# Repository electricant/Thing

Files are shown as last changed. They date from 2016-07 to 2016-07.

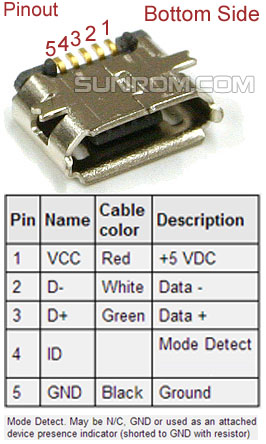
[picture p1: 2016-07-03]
board/datasheet/micro-usb-pinout.jpg

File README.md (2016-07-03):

# Thing

Final projects for Robotics exam.

# Objectives

The goal of this project is designing a board to control 5 servomotors,
one for each finger of a [robotic hand](http://inmoov.fr/hand-and-forarm/).
The heart of the project is an atXmega microcontoller which should be able
to set both the current, the angle and the speed of each servo individually.
The hand is also capable of holding things with a user-specified force.

Everything is battery powered and commands can be sent via a WiFi link or
through an USB port. A [ROS](http://www.ros.org/) module will be provided for 
integration with existing or new robotics projects.

A programmer is included within the board for easy firmware upgrade.

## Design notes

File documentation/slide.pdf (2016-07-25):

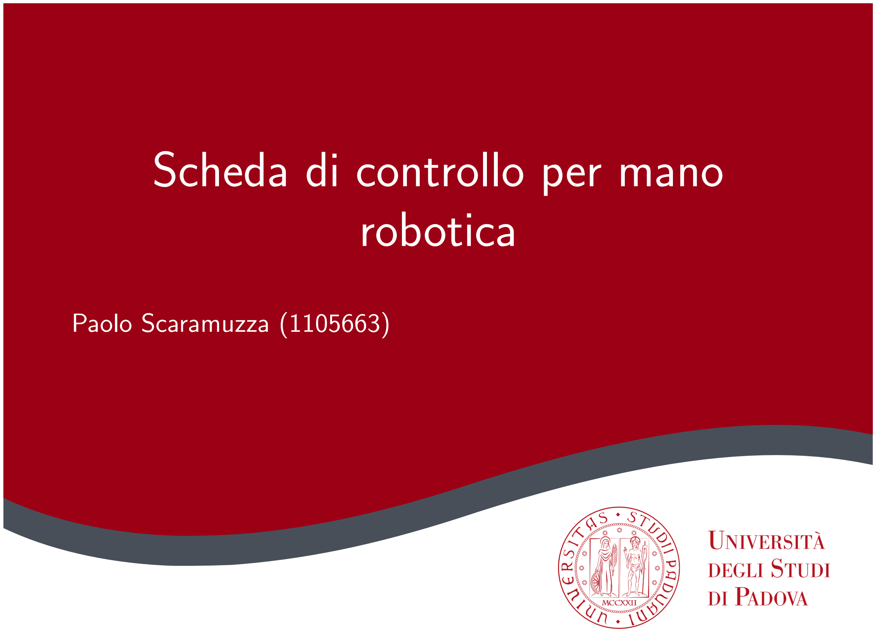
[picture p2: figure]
Scheda di controllo per mano robotica; Paolo Scaramuzza (1105663)

## Contenuti

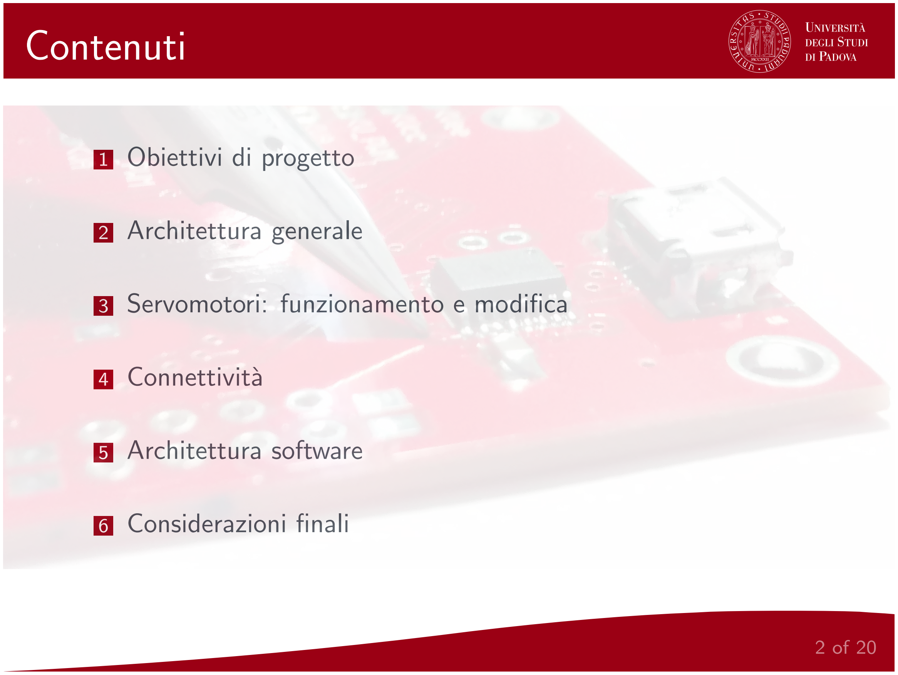
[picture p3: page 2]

1 | Obiettivi di progetto
2 | Architettura generale
3 | Servomotori: funzionamento e modifica
4 | Connettivit`a
5 | Architettura software
6 | Considerazioni finali

## Obiettivi di progetto

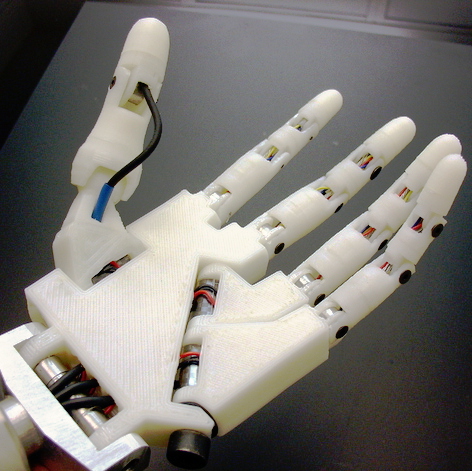
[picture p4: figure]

Controllo di angolo, velocit`a e forza di 5 servomotori
Rate di aggiornamento
≥ 100Hz

Alimentazione a batteria
Controllo WiFi e USB
Facilit`a d’uso e
programmazione

## Architettura generale

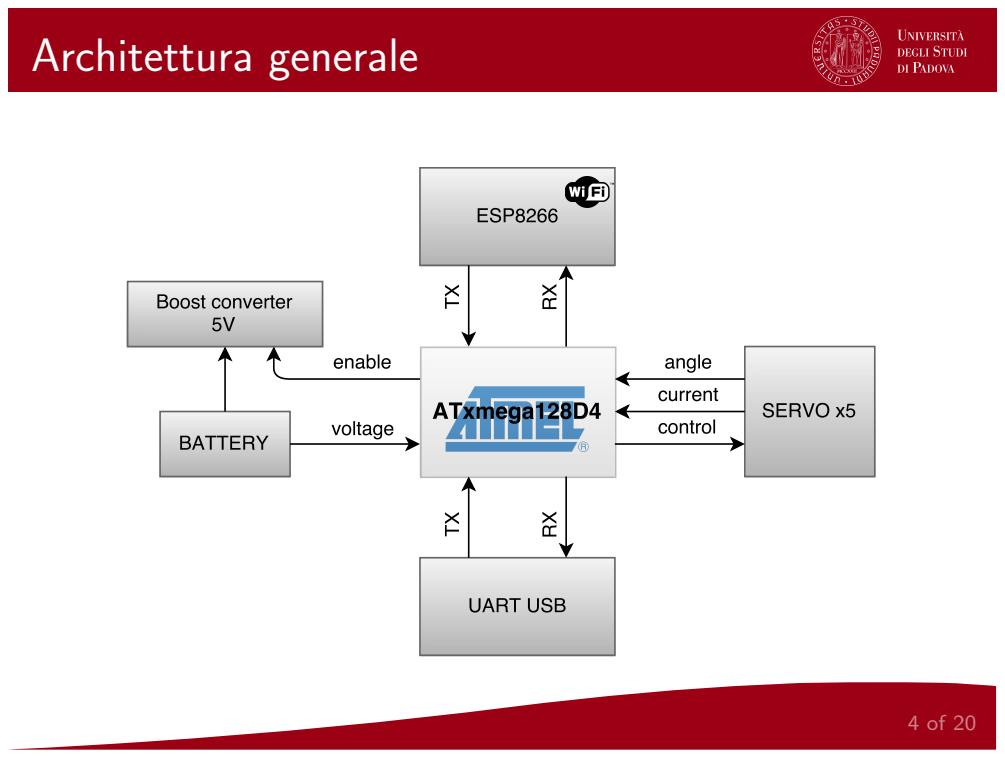
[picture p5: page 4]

## Servomotori - Funzionamento

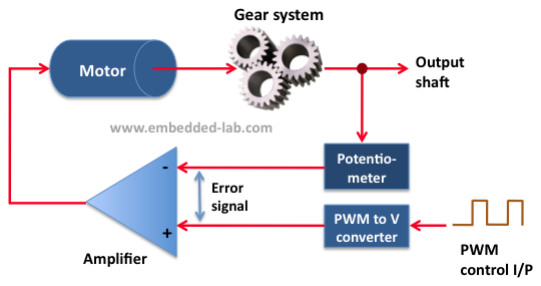
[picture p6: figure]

Sistema in feedback
Facile controllo
Non conosco l’angolo effettivo

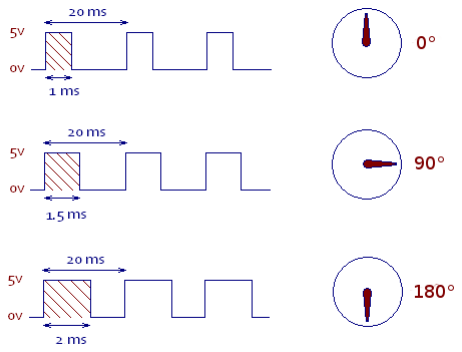
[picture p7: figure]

Non conosco la corrente assorbita (sforzo)

## Servomotori - Lettura dell’angolo

IDEA: loop di controllo esterno (microcontrollore)

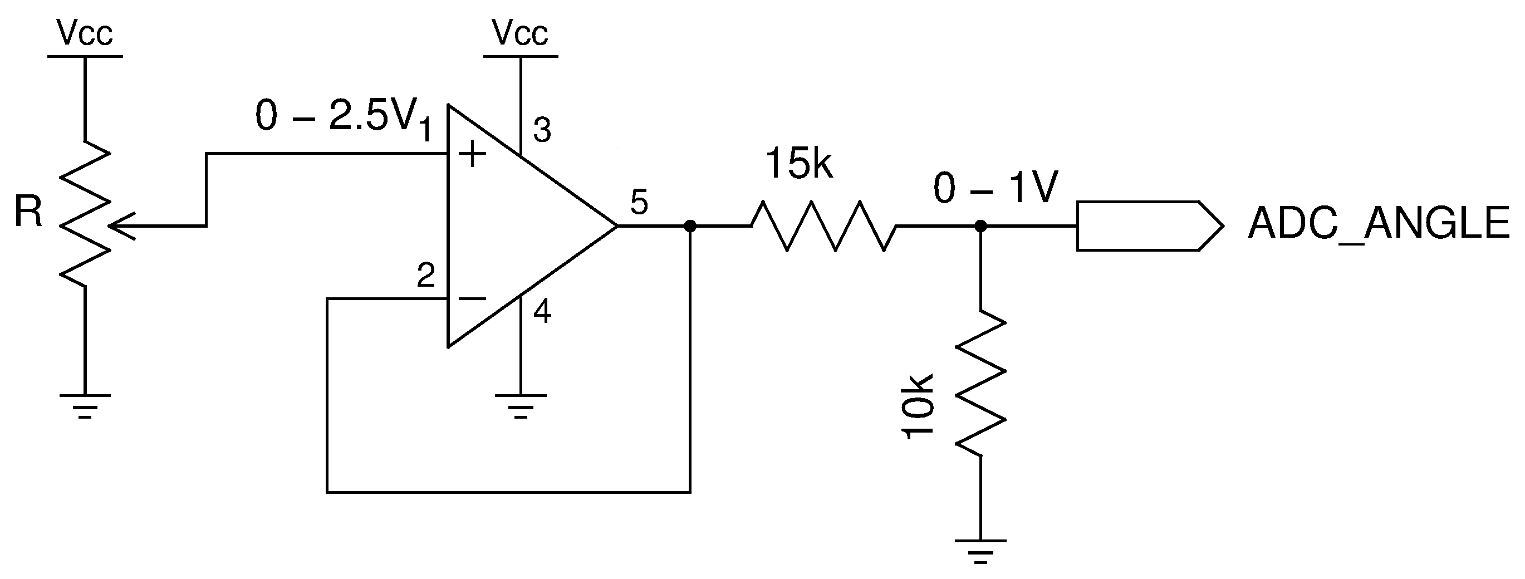
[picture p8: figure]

VADC = VA ·

10k
10k + 15k

=

α
180◦

Non assorbire corrente dal potenziometro!

## Servomotori - Lettura della corrente

IDEA: loop di controllo esterno (microcontrollore)

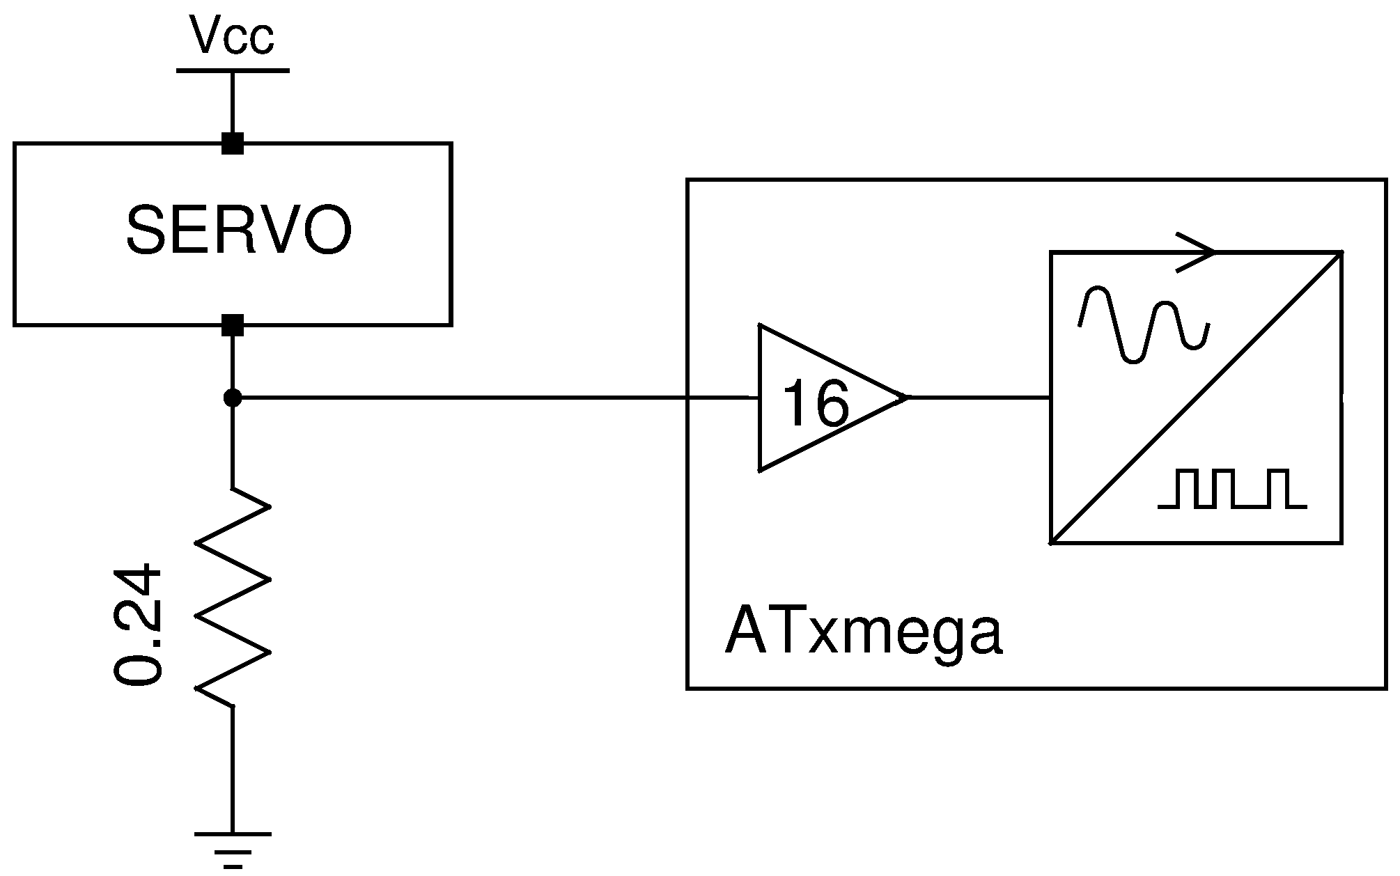
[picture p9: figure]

VADC = 16 · 0.24 · I

s ≈

1V
256
- I

(mA)
s

Errore sistematico (correggibile) pari all’1, 54%

## ESP8266

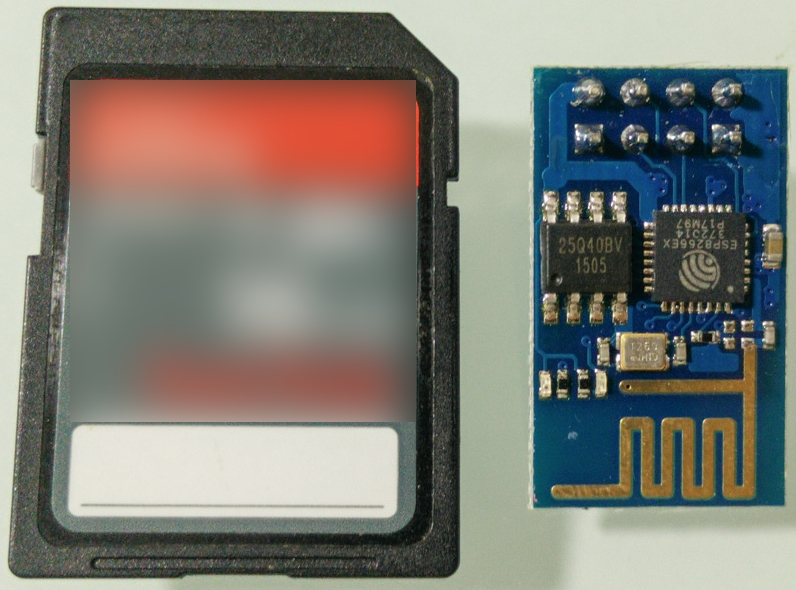
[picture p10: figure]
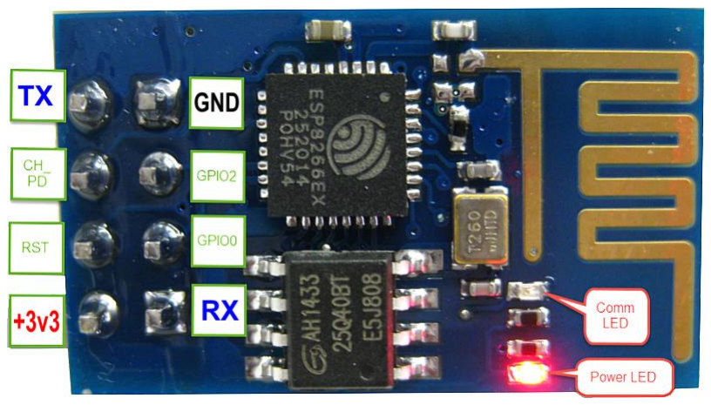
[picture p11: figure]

Prodotta da Espressif (Shanghai)

Molto diffusa tra i makers
IEEE 802.11 b/g/n Wi-Fi con stack TCP/IP completo 80 MHz 32bit RISC CPU (Tensilica Xtensa LX106)

## ESP8266 - Funzionamento e comandi

Alimentazione: 2,5 - 3,3V 150mA (≈ 0, 5W )

Interfaccia seriale 115200baud (modificabile)

Set di comandi Hayes (AT - attention)

AT+<comando><CR><LF>

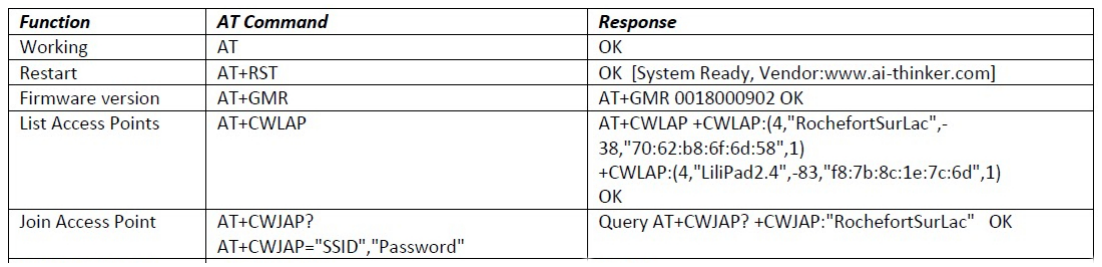
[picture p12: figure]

## Adattatore seriale USB

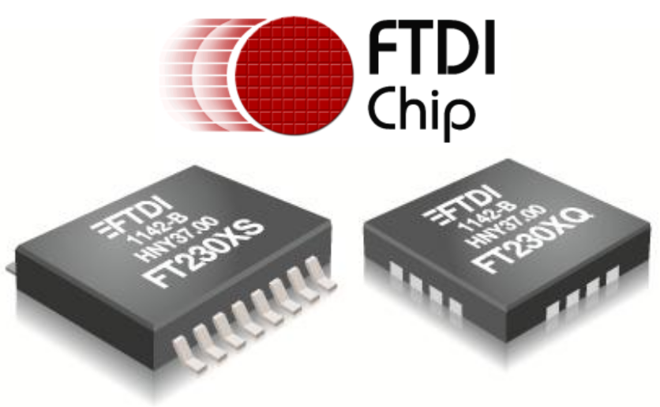
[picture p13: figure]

Pochi componenti esterni (capacit`a di bypass)

Alimentazione: 1,8 - 5V 8mA (≈ 40mW )

Da 300 a 3M baud con o senza parit`a

USB product name e manufacturer configurabili

## Scheda elettrica

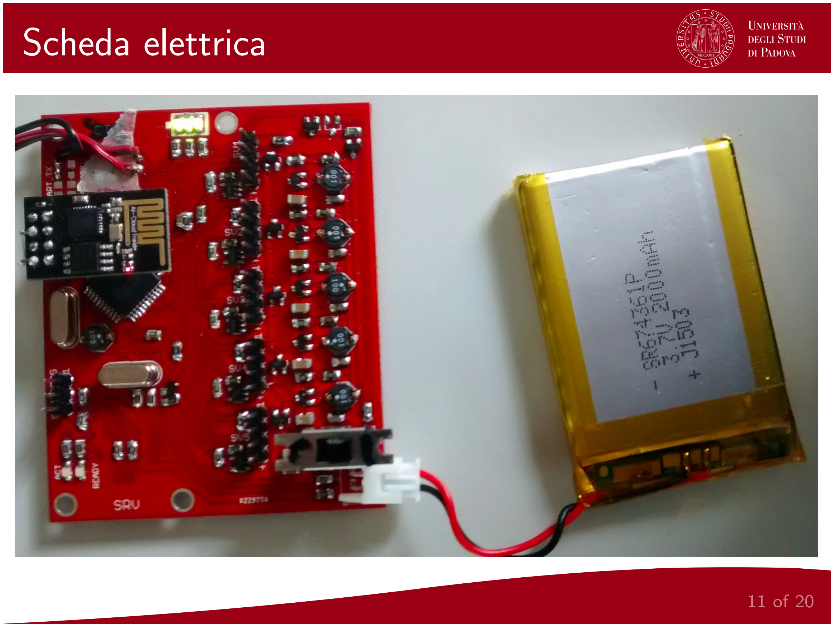
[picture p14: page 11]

## Architettura software

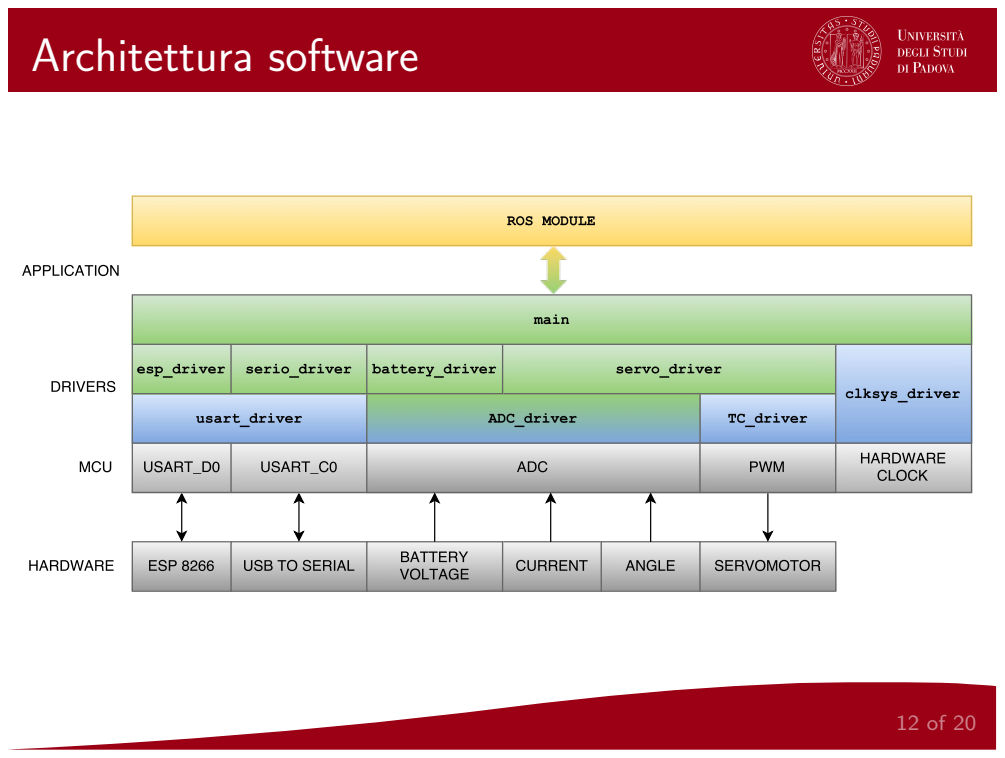
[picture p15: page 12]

## esp driver

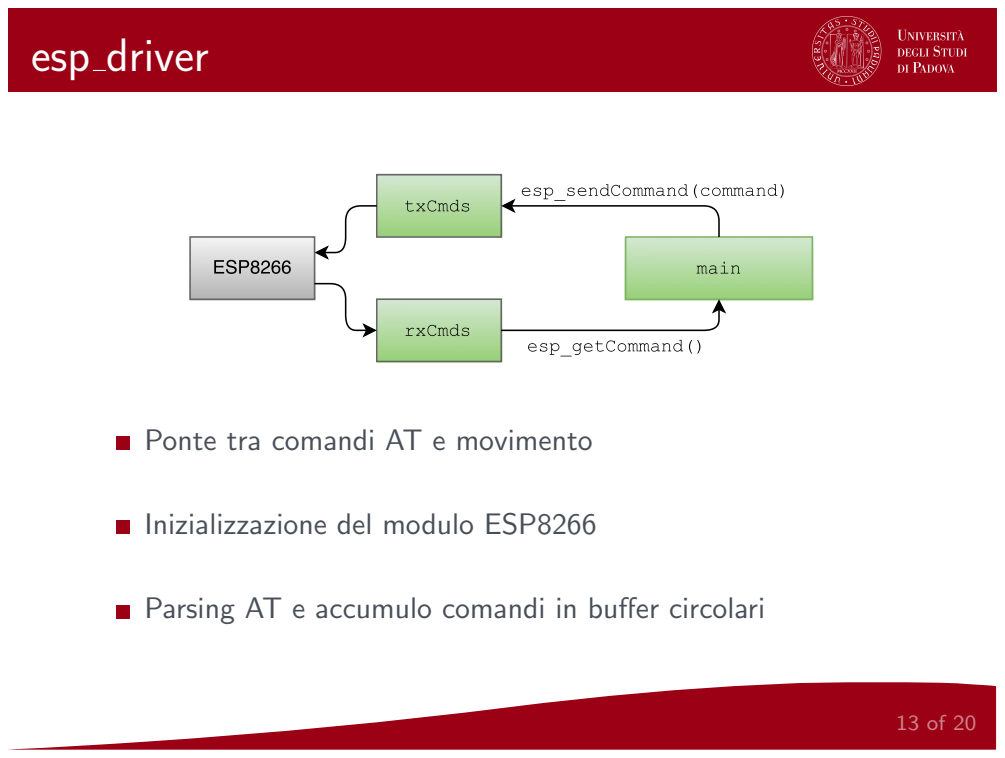
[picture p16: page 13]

Ponte tra comandi AT e movimento

Inizializzazione del modulo ESP8266

Parsing AT e accumulo comandi in buffer circolari

## esp driver - Comandi

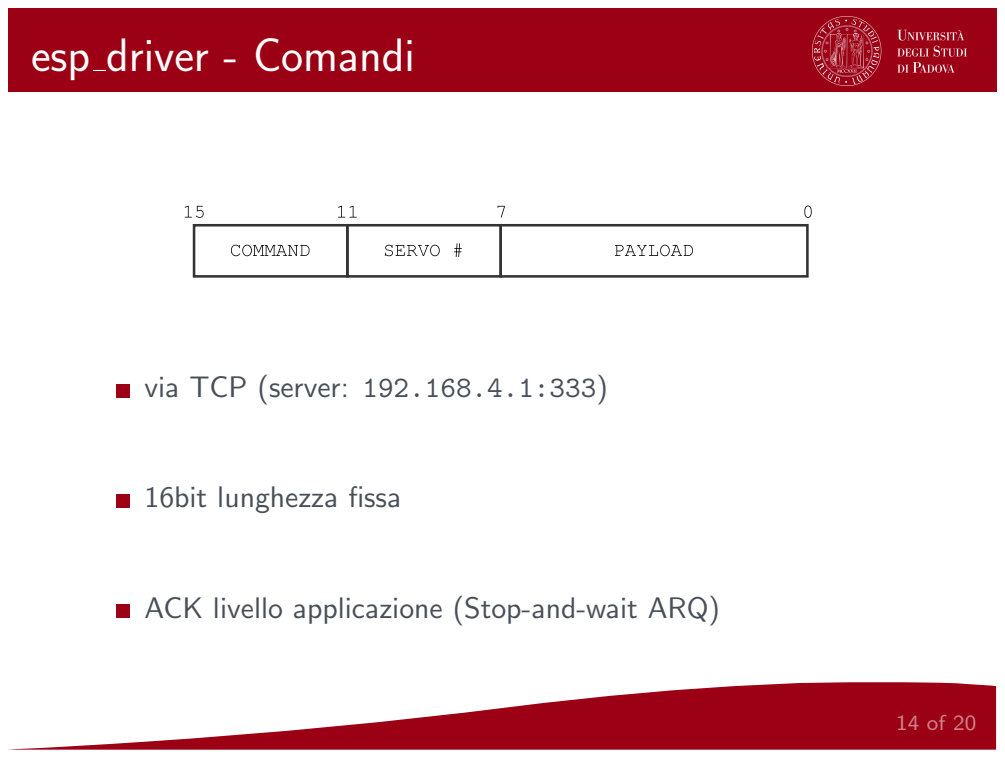
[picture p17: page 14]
16bit lunghezza fissa

via TCP (server: 192.168.4.1:333)

ACK livello applicazione (Stop-and-wait ARQ)

## serio driver

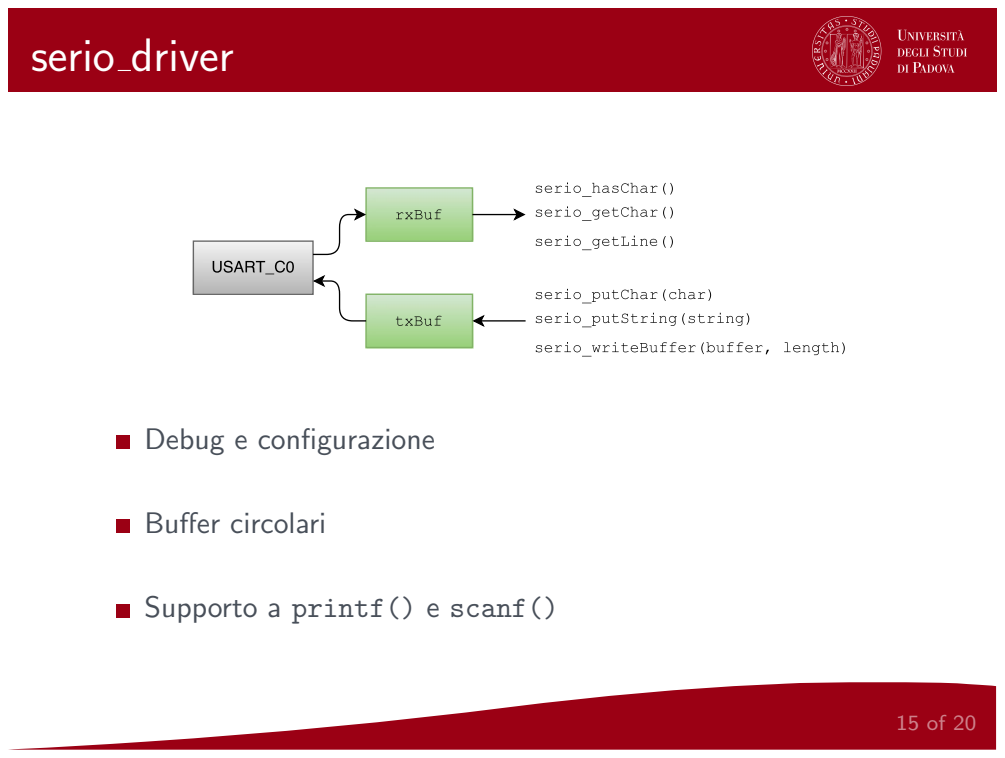
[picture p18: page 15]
Debug e configurazione; Buffer circolari

Supporto a printf() e scanf()

## battery driver

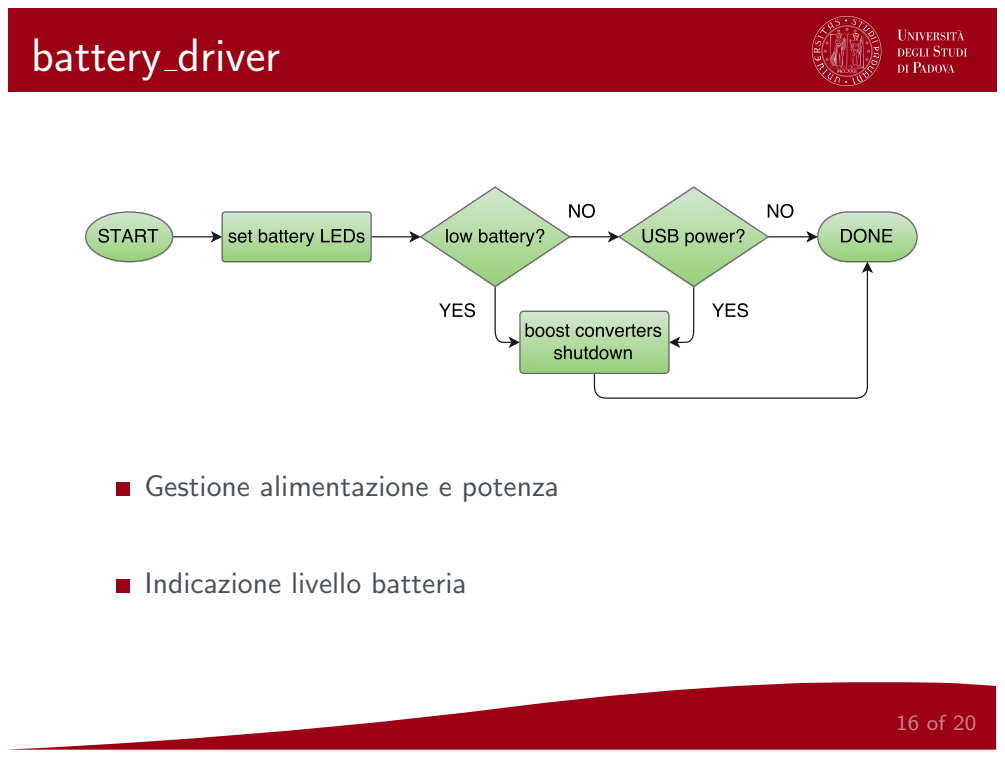
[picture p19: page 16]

Gestione alimentazione e potenza

Indicazione livello batteria

## adc driver

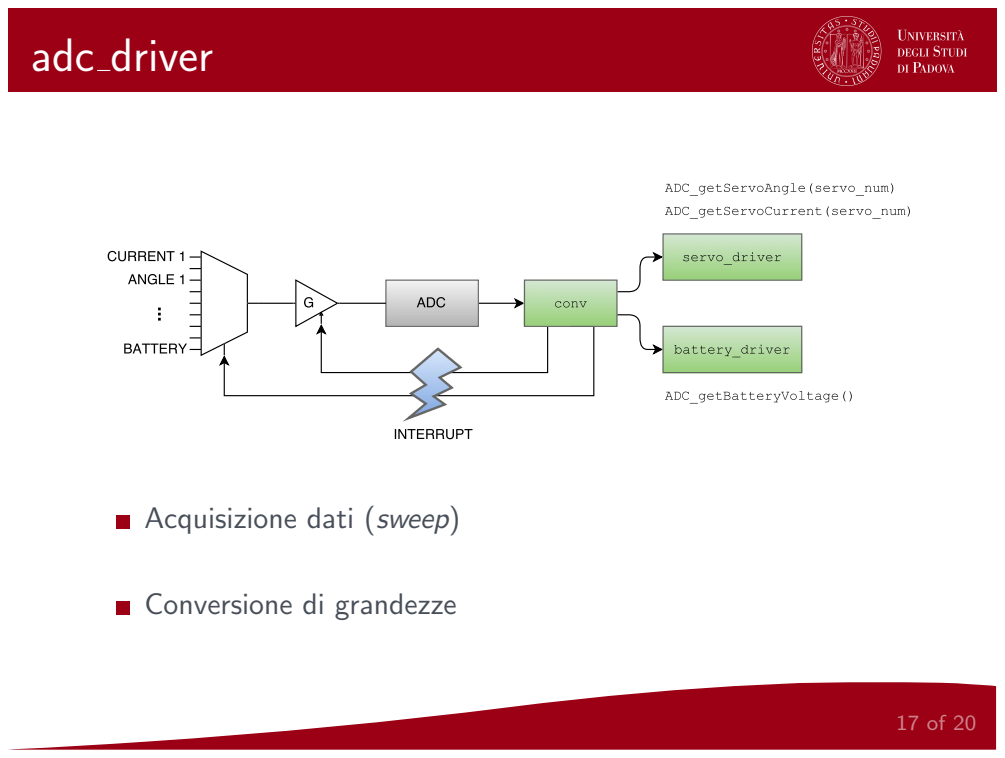
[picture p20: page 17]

Acquisizione dati (sweep)

Conversione di grandezze

## servo driver

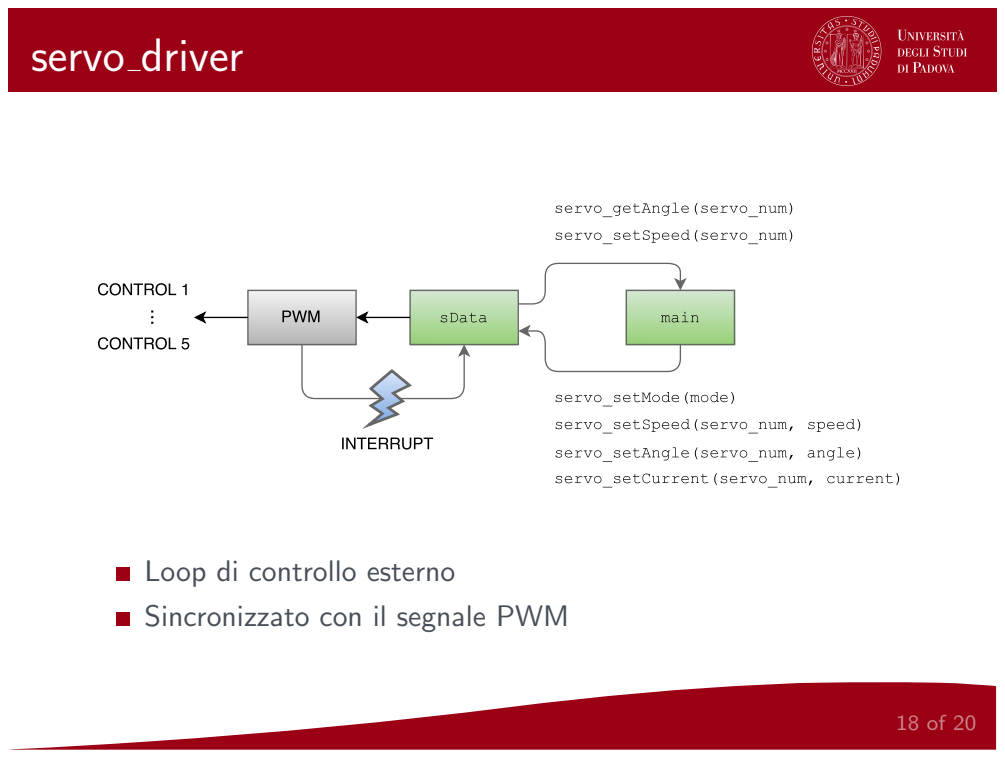
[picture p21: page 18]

Loop di controllo esterno
Sincronizzato con il segnale PWM

## servo driver - Modalit`a operative

Singolo motore: Forza (corrente), velocit`a e angolo

Globalmente:

FOLLOW −→ ”mano morta”

ANGLE −→ raggiunge una posizione con velocit`a imposta

HOLD −→ stringe oggetti con forza nota

## Conclusioni

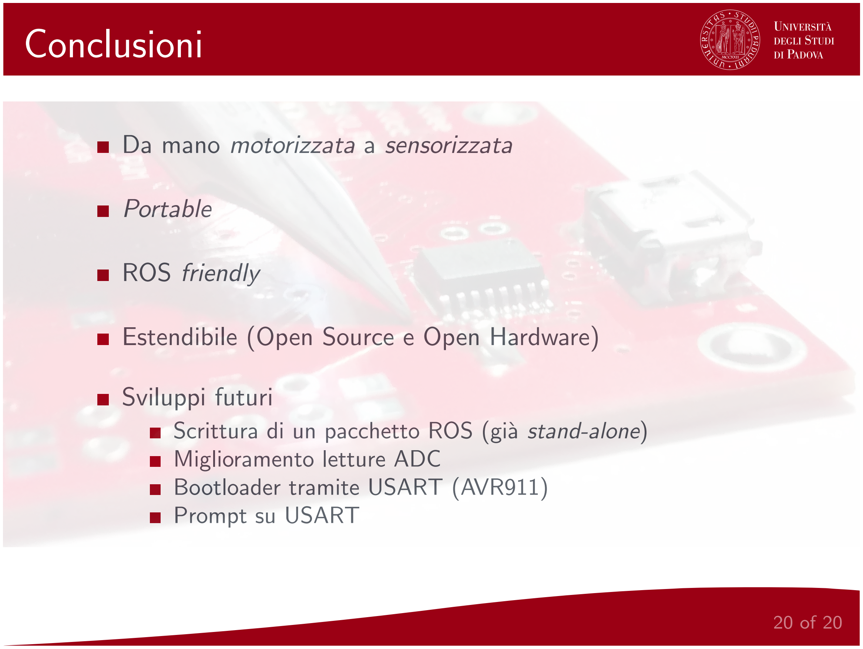
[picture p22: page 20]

Da mano motorizzata a sensorizzata

Portable

ROS friendly

Estendibile (Open Source e Open Hardware)

Sviluppi futuri
Scrittura di un pacchetto ROS (gi`a stand-alone) Miglioramento letture ADC
Bootloader tramite USART (AVR911)
Prompt su USART

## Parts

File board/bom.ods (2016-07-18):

Oggetto | Descrizione | Quantità richiesta | Acquistati | Costo unitario | Link | Note | Costo totale | Presente in laboratorio
 | batteria 3,7V | 1 | 1 | 14,29 | link (http://it.rs-online.com/web/p/pacchi-batteria-al-litio-ricaricabili/7916460/) | batteria al litio rettangolare 3,7V 2000mAh | 14,29
 | Boost converter 1A | 5 | 6 | 1,02 | link (http://it.rs-online.com/web/p/convertitori-boost/7546402/) | MIC2250 | 6,12
 | condensatore 100nF | 11 | 50 | 0,004 | link (http://it.rs-online.com/web/p/condensatori-ceramici-multistrato/0390990/) | Ne avanzeranno un pochi. | 0,2
 | condensatore 10uF SMD | 8 | 10 | 0,069 | link (http://it.rs-online.com/web/p/condensatori-ceramici-multistrato/6983734/) |  | 0,69 | un sacco da 4,7u
 | condensatori 47pF | 2 | 25 | 0,023 | link (http://it.rs-online.com/web/p/condensatori-ceramici-multistrato/2644270/) | Qui ne avanzeranno di più | 0,575
 | condensatori quarzo 27pF | 4 | 5 | 0,27 | link (http://it.rs-online.com/web/p/condensatori-ceramici-multistrato/6984064/) | Suppongo 5pF di capacità sui piedini. CL= 18pF | 1,35 | si 4
 | connettore batteria maschio | 1 | 5 | 0,114 | link (http://it.rs-online.com/web/p/file-di-contatti-da-pcb/8201582/) | JST-XHP-2 per PCB ad angolo retto (più carino) | 0,57
 | connettore batteria femmina | 1 | 0 | 0 |  | 2 pin, difficile da invertire, già sulla batteria | 0
 | connettore servo femmina filo | tanti | 0 | 0 |  | pin singolo per filo di sensing, usare cavi arduino con presa femmina |  | si tanti
 | connettore servo maschio | 5 | 10 | 0,116 | LINK (http://it.rs-online.com/web/p/file-di-contatti-da-pcb/6812988/) | 4 pin. Scrivere sul PCB la funzione di ciascun PIN | 1,16 | si in abbondanza
 | controller carica batteria | 1 | 5 | 0,51 | link (http://it.rs-online.com/web/p/controller-carica-di-batterie/7386617/) | MCP73831-2 | 2,55
 | convertitore LDO 3,3V | 1 | 25 | 0,122 | link (http://it.rs-online.com/web/p/regolatori-di-tensione-low-dropout/8855980/) | MIC5504-3.3 oppure SP6201EM5-3.3 | 3,05
 | convertitore seriale-usb | 1 | 2 | 1,86 | link (http://it.rs-online.com/web/p/trasmettitori-e-ricevitori-universali-asincroni/7570010/) | FT230XS-R | 3,72
 | diodo shottky 1A | 12 | 20 | 0,039 | link (http://it.rs-online.com/web/p/diodi-rettificatori-e-schottky/0508977/) | package SOT-23 | 0,78
 | ESP8266 | 1 | 0 | 0 |  | Ce lo metto di mio che si fa prima | 0
 | header ICSP | 1 | 5 | 0,304 | link (http://it.rs-online.com/web/p/file-di-contatti-da-pcb/6737503/) | 6pin Header Connector with 2.54mm (100 MIL) spacing (con quelli che avanzano TP UART) | 1,52 | si in abbondanza
 | Induttori boost 10uH | 6 | 10 | 0,288 | link (http://it.rs-online.com/web/p/induttori-avvolti-smd/7381211/) |  | 2,88
 | LED verde | 7 | 50 | 0,05 | linik (http://it.rs-online.com/web/p/led-visibili/6545773/) | TX + RX seriale, programmatore e livello batteria | 2,5 | si 5 color rosso
 | microcontrollore AT90USB162 | 1 | 1 | 3,82 | link (http://it.rs-online.com/web/p/microcontroller/7153750/) | per programmare la board via usb. Vedi AVR-ISP-MK2 (https://www.olimex.com/Products/AVR/Programmers/AVR-ISP-MK2/open-source-hardware) | 3,82
 | microcontrollore ATxmega128D4 | 1 | 1 | 4,02 | link (http://it.rs-online.com/web/p/microcontroller/7153873/) |  | 4,02
 | opamp MCP6L01T-E/OT | 5 | 10 | 0,221 | link (http://it.rs-online.com/web/p/amplificatori-operazionali/7386196/) |  | 2,21
 | PCB | 1 | 0 | 0 |  | Ce lo metto di mio che si fa prima | 0
 | porte micro usb | 2 | 5 | 0,426 | link (http://it.rs-online.com/web/p/connettori-micro-usb/7142344/) |  | 2,13
 | quarzo 16MHz | 2 | 10 | 0,167 | link (http://it.rs-online.com/web/p/cristalli/8149440/) | Tutti e due i micro usano un quarzo. Per il principale vedi come si configura e usa | 1,67
 | resistenza 0,24 Ohm 1% | 5 | 5 | 0,182 | link (http://it.rs-online.com/web/p/resistori-smd/7215423/) | sensing di corrente | 0,91 | 8 da 0,1Ohm
 | resistenza 100 Ohm | 9 | 50 | 0,01 | link (http://it.rs-online.com/web/p/resistori-smd/7408978/) | PDI + LED batteria (due in parallelo) | 0,5
 | resistenza 100kOhm | 6 | 50 | 0,01 | link (http://it.rs-online.com/web/p/resistori-smd/2230691/) |  | 0,5
 | resistenza 10kOhm 1% | 12 | 50 | 0,006 | link (http://it.rs-online.com/web/p/resistori-smd/2230584/) |  | 0,3 | si un sacco
 | resistenza 15kOhm 1% | 5 | 50 | 0,016 | link (http://it.rs-online.com/web/p/resistori-smd/7408975/) |  | 0,8 | si un sacco
 | resistenza 18kOhm | 2 | 50 | 0,023 | link (http://it.rs-online.com/web/p/resistori-smd/2230590/) |  | 1,15
 | resistenza 2,2kOhm | 1 | 50 | 0,034 | link+ (http://it.rs-online.com/web/p/resistori-smd/6791207/) |  | 1,7 | si un sacco
 | resistenza 22 Ohm | 2 | 50 | 0,006 | link (http://it.rs-online.com/web/p/resistori-smd/2230203/) |  | 0,3 | si un sacco
 | resistenza 27 Ohm | 2 | 50 | 0,016 | link (http://it.rs-online.com/web/p/resistori-smd/6791187/) |  | 0,8
 | resistenza 330 Ohm | 9 | 50 | 0,017 | link (http://it.rs-online.com/web/p/resistori-smd/7409022/) |  | 0,85
 | resistenza 330kOhm | 1 | 50 | 0,01 | link (http://it.rs-online.com/web/p/resistori-smd/6791272/) |  | 0,5
 | resistenza 33kOhm | 5 | 50 | 0,021 | link (http://it.rs-online.com/web/p/resistori-smd/2230629/) |  | 1,05 | si 3
 | switch batteria | 1 | 1 | 2,49 | link (http://it.rs-online.com/web/p/interruttori-a-slitta/7118385/) | 4 A 20mOhm | 2,49
 | switch programmazione NA | 2 | 0 | 0 |  | RESET + HWB (vedi qui) - Ne porto da casa (http://www.atmel.com/Images/doc7627.pdf) | 0
 | transistor NPN SMD | 1 | 0 | 0 |  | Me lo porto da casa | 0
 |  |  |  |  |  |  | TOTALE:
 |  |  |  |  |  |  | 67,655
 |  |  |  |  |  |  | TOTALE + IVA
 |  |  |  |  |  |  | 82,5391

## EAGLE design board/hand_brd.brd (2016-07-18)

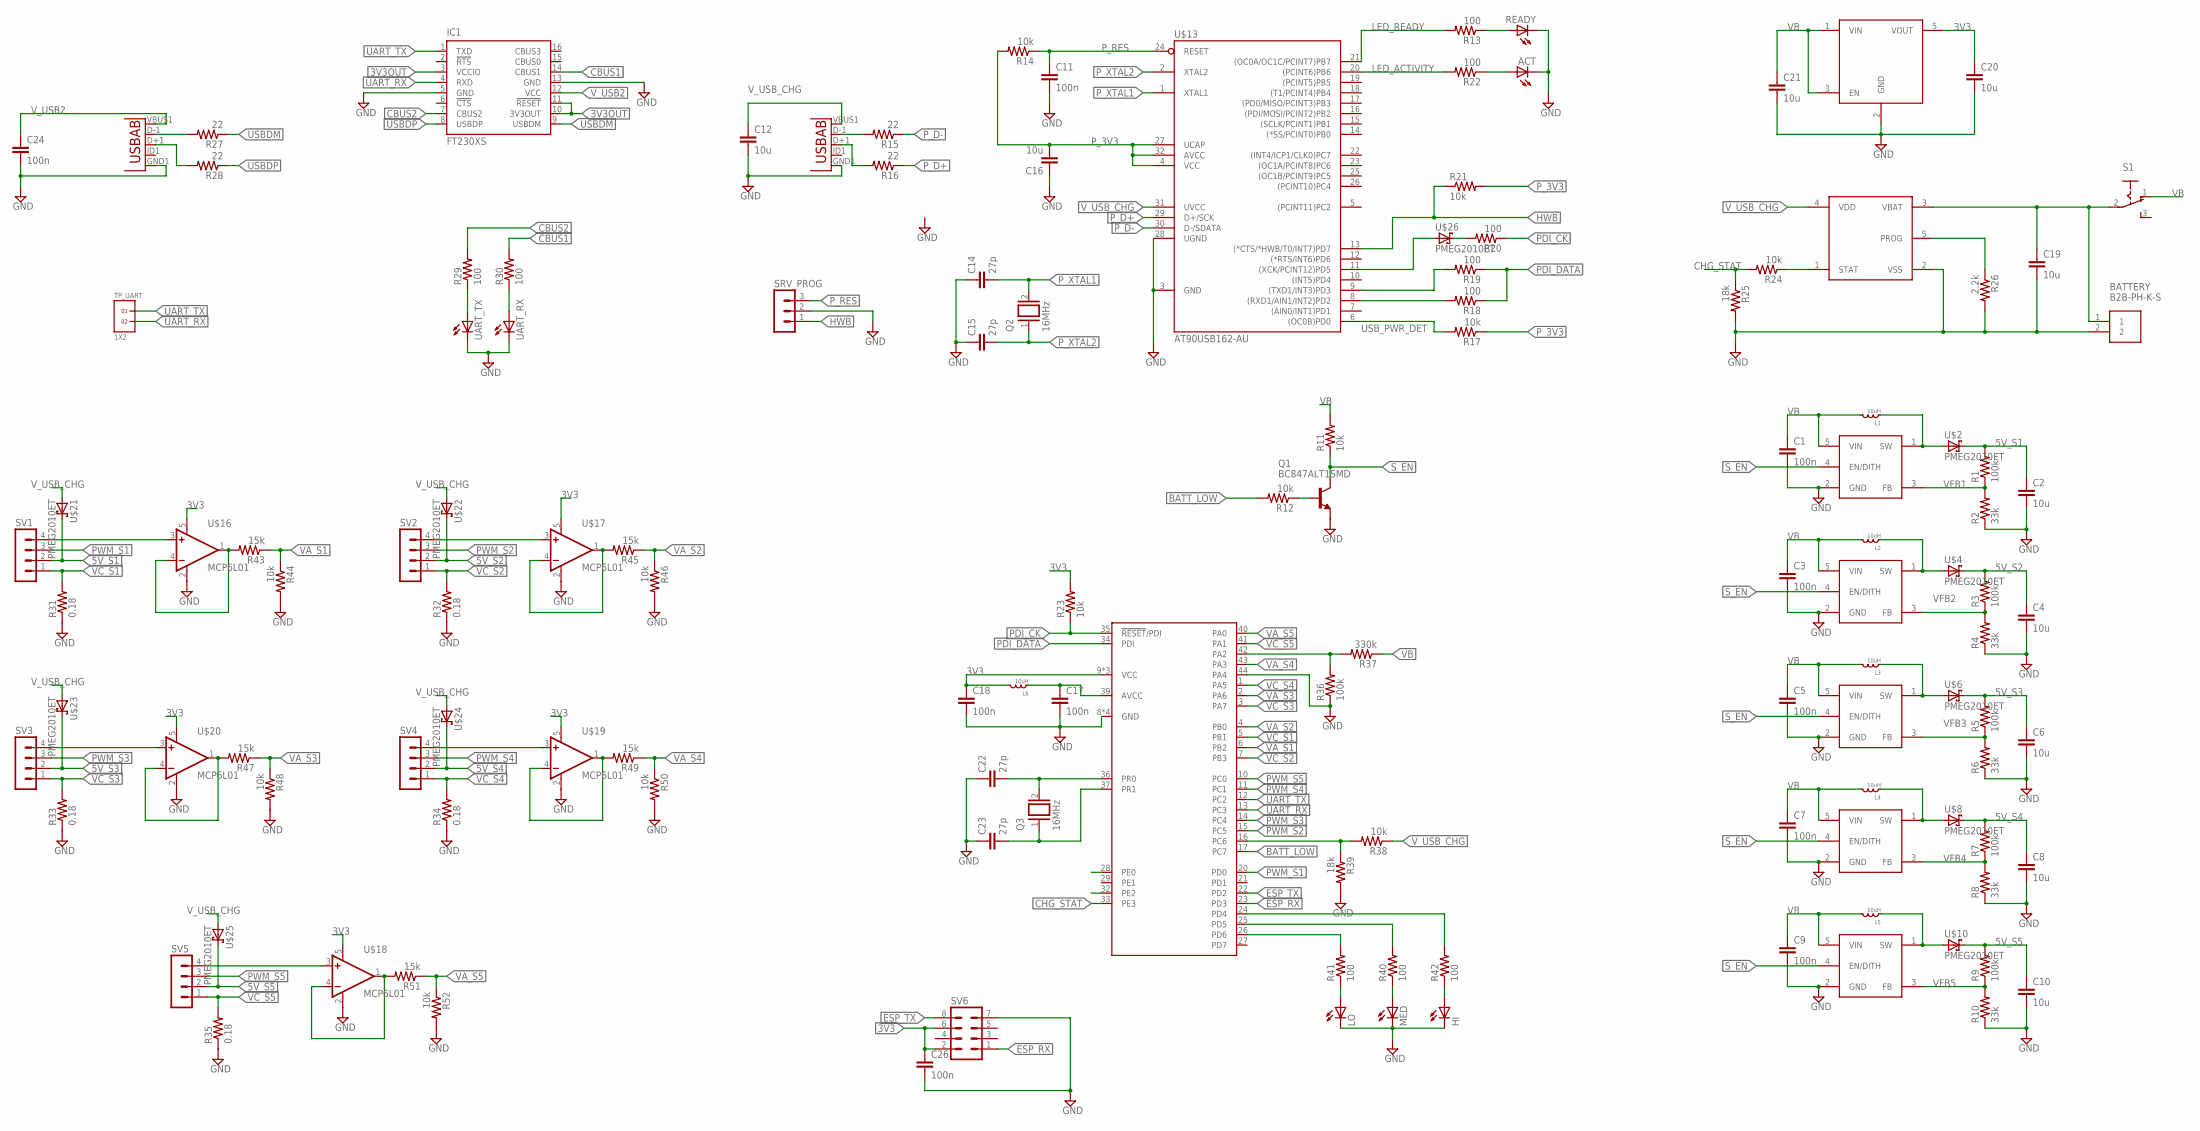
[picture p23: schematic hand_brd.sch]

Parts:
ACT: LEDCHIPLED_0805; CHIPLED_0805
BATTERY: B2B-PH-K-S
C1, C3, C5, C7, C9, C11, C17, C18, C24, C26: 100n; C0805K
C2, C4, C6, C8, C10, C12, C16, C19, C20, C21: 10u; C0805K
C14, C15, C22, C23: 27p; C0805K
HI: LEDCHIPLED_0805; CHIPLED_0805
IC1: FT230XS; SSOP16
L1, L2, L3, L4, L5, L6: 10uH; LTF5022
LO: LEDCHIPLED_0805; CHIPLED_0805
MED: LEDCHIPLED_0805; CHIPLED_0805
Q1: BC847ALT1SMD; SOT23
Q2, Q3: 16MHz; QS
R1, R3, R5, R7, R9, R36: 100k; M0805
R2, R4, R6, R8, R10: 33k; M0805
R11, R12, R14, R17, R21, R23, R24, R38, R44, R46, R48, R50, R52: 10k; M0805
R13, R18, R19, R20, R22, R29, R30, R40, R41, R42: 100; M0805
R15, R16, R27, R28: 22; M0805
R25, R39: 18k; M0805
R26: 2.2k; M0805
R31, R32, R33, R34, R35: 0.18; M0805
R37: 330k; M0805
R43, R45, R47, R49, R51: 15k; M0805
READY: LEDCHIPLED_0805; CHIPLED_0805
S1: 255SB
SRV_PROG: MA03-1
SV1, SV2, SV3, SV4, SV5: MA04-1
SV6: MA04-2
TP_UART: 1X2
U1, U3: USB""; USB-MICRO-SMD
U2: ATXMEGA128D4-AU; TQFP-44A-44
U$1, U$3, U$5, U$7, U$9: MIC2250-2YD5; SOT23-5
U$2, U$4, U$6, U$8, U$10, U$21, U$22, U$23, U$24, U$25, U$26: PMEG2010ET; SOT23
U$13: AT90USB162-AU; TQFP32-08
U$14: MCP73831; SOT23-5
U$15: MIC5504; SOT23-5
U$16, U$17, U$18, U$19, U$20: MCP6L01; SOT23-5
UART_RX: LEDCHIPLED_0805; CHIPLED_0805
UART_TX: LEDCHIPLED_0805; CHIPLED_0805

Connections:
3V3: C18.1, C20.1, C26.1, L6.P$2 (2), R23.2, SV6.2, SV6.6, U2.9 (VCC), U2.19 (VCC), U2.31 (VCC), U$15.5 (VOUT), U$16.5 (V+), U$17.5 (V+), U$18.5 (V+), U$19.5 (V+), U$20.5 (V+)
3V3OUT: IC1.3 (VCCIO), IC1.10 (3V3OUT), IC1.11 (!RESET)
5V_S1: C2.1, R1.2, SV1.2, U$2.3 (C), U$21.3 (C)
5V_S2: C4.1, R3.2, SV2.2, U$4.3 (C), U$22.3 (C)
5V_S3: C6.1, R5.2, SV3.2, U$6.3 (C), U$23.3 (C)
5V_S4: C8.1, R7.2, SV4.2, U$8.3 (C), U$24.3 (C)
5V_S5: C10.1, R9.2, SV5.2, U$10.3 (C), U$25.3 (C)
BATT_LOW: R12.2, U2.17 (PC7)
CBUS1: IC1.14 (CBUS1), R30.2
CBUS2: IC1.7 (CBUS2), R29.2
CHG_STAT: R24.2, R25.1, U2.33 (PE3)
ESP_RX: SV6.1, U2.23 (PD3)
ESP_TX: SV6.8, U2.22 (PD2)
GND: ACT.C, BATTERY.2, C1.2, C2.2, C3.2, C4.2, C5.2, C6.2, C7.2, C8.2, C9.2, C10.2, C11.2, C12.2, C14.1, C15.1, C16.1, C17.2, C18.2, C19.2, C20.2, C21.2, C22.1, C23.1, C24.2, C26.2, HI.C, IC1.5 (GND), IC1.13 (GND), LO.C, MED.C, Q1.2 (E), R2.1, R4.1, R6.1, R8.1, R10.1, R25.2, R26.2, R31.1, R32.1, R33.1, R34.1, R35.1, R36.1, R39.2, R44.2, R46.2, R48.2, R50.2, R52.2, READY.C, SRV_PROG.2, SV6.7, U1.GND1 (GND), U2.8 (GND), U2.18 (GND), U2.30 (GND), U2.38 (GND), U2.44 (PA4), U3.GND1 (GND), U$1.2 (GND), U$3.2 (GND), U$5.2 (GND), U$7.2 (GND), U$9.2 (GND), U$13.3 (GND), U$13.28 (UGND), U$14.2 (VSS), U$15.2 (GND), U$16.2 (V-), U$17.2 (V-), U$18.2 (V-), U$19.2 (V-), U$20.2 (V-), UART_RX.C, UART_TX.C
HWB: R21.1, SRV_PROG.1, U$13.13 ((*CTS/*HWB/T0/INT7)PD7)
LED_ACTIVITY: R22.2, U$13.20 ((PCINT6)PB6)
LED_READY: R13.2, U$13.21 ((OC0A/OC1C/PCINT7)PB7)
unnamed: L2.P$1 (1), U$3.1 (SW), U$4.1 (A)
unnamed: L1.P$1 (1), U$1.1 (SW), U$2.1 (A)
unnamed: R18.2, U$13.8 ((RXD1/AIN1/INT2)PD2)
unnamed: L3.P$1 (1), U$5.1 (SW), U$6.1 (A)
unnamed: Q1.1 (B), R12.1
unnamed: L4.P$1 (1), U$7.1 (SW), U$8.1 (A)
unnamed: R16.2, U3.D+1 (D+)
unnamed: L5.P$1 (1), U$9.1 (SW), U$10.1 (A)
unnamed: R15.2, U3.D-1 (D-)
unnamed: R20.2, U$26.3 (C)
unnamed: R19.2, U$13.9 ((TXD1/INT3)PD3)
unnamed: U$13.11 ((XCK/PCINT12)PD5), U$26.1 (A)
unnamed: R13.1, READY.A
unnamed: ACT.A, R22.1
unnamed: C17.1, L6.P$1 (1), U2.39 (AVCC)
unnamed: R27.2, U1.D-1 (D-)
unnamed: R24.1, U$14.1 (STAT)
unnamed: R26.1, U$14.5 (PROG)
unnamed: BATTERY.1, C19.1, S1.2, U$14.3 (VBAT)
unnamed: R28.2, U1.D+1 (D+)
unnamed: R29.1, UART_TX.A
unnamed: R30.1, UART_RX.A
unnamed: R36.2, R37.2, U2.42 (PA2)
unnamed: R38.2, R39.1, U2.16 (PC6)
unnamed: SV2.4, U$17.3 (+IN)
unnamed: SV1.4, U$16.3 (+IN)
unnamed: SV5.4, U$18.3 (+IN)
unnamed: MED.A, R40.1
unnamed: SV3.4, U$20.3 (+IN)
unnamed: SV4.4, U$19.3 (+IN)
unnamed: LO.A, R41.1
unnamed: HI.A, R42.1
unnamed: R41.2, U2.26 (PD6)
unnamed: R40.2, U2.25 (PD5)
unnamed: R42.2, U2.24 (PD4)
unnamed: R45.2, U$17.1 (OUT), U$17.4 (-IN)
unnamed: R43.2, U$16.1 (OUT), U$16.4 (-IN)
unnamed: R47.2, U$20.1 (OUT), U$20.4 (-IN)
unnamed: R49.2, U$19.1 (OUT), U$19.4 (-IN)
unnamed: R51.2, U$18.1 (OUT), U$18.4 (-IN)
PDI_CK: R20.1, R23.1, U2.35 (!RESET!/PDI)
PDI_DATA: R18.1, R19.1, U2.34 (PDI)
PWM_S1: SV1.3, U2.20 (PD0)
PWM_S2: SV2.3, U2.15 (PC5)
PWM_S3: SV3.3, U2.14 (PC4)
PWM_S4: SV4.3, U2.11 (PC1)
PWM_S5: SV5.3, U2.10 (PC0)
P_3V3: C16.2, R14.2, R17.1, R21.2, U$13.4 (VCC), U$13.27 (UCAP), U$13.32 (AVCC)
P_D+: R16.1, U$13.29 (D+/SCK)
P_D-: R15.1, U$13.30 (D-/SDATA)
P_RES: C11.1, R14.1, SRV_PROG.3, U$13.24 (RESET)
P_XTAL1: C14.2, Q2.2, U$13.1 (XTAL1)
P_XTAL2: C15.2, Q2.1, U$13.2 (XTAL2)
S_EN: Q1.3 (C), R11.1, U$1.4 (EN/DITH), U$3.4 (EN/DITH), U$5.4 (EN/DITH), U$7.4 (EN/DITH), U$9.4 (EN/DITH)
UART_RX: IC1.4 (RXD), TP_UART.2, U2.13 (PC3)
UART_TX: IC1.1 (TXD), TP_UART.1, U2.12 (PC2)
USBDM: IC1.9 (USBDM), R27.1
USBDP: IC1.8 (USBDP), R28.1
USB_PWR_DET: R17.2, U$13.6 ((OC0B)PD0)
VA_S1: R43.1, R44.1, U2.6 (PB2)
VA_S2: R45.1, R46.1, U2.4 (PB0)
VA_S3: R47.1, R48.1, U2.2 (PA6)
VA_S4: R49.1, R50.1, U2.43 (PA3)
VA_S5: R51.1, R52.1, U2.40 (PA0)
VB: C1.1, C3.1, C5.1, C7.1, C9.1, C21.1, L1.P$2 (2), L2.P$2 (2), L3.P$2 (2), L4.P$2 (2), L5.P$2 (2), R11.2, R37.1, S1.1 (O), U$1.5 (VIN), U$3.5 (VIN), U$5.5 (VIN), U$7.5 (VIN), U$9.5 (VIN), U$15.1 (VIN), U$15.3 (EN)
VC_S1: R31.2, SV1.1, U2.5 (PB1)
VC_S2: R32.2, SV2.1, U2.7 (PB3)
VC_S3: R33.2, SV3.1, U2.3 (PA7)
VC_S4: R34.2, SV4.1, U2.1 (PA5)
VC_S5: R35.2, SV5.1, U2.41 (PA1)
VFB1: R1.1, R2.2, U$1.3 (FB)
VFB2: R3.1, R4.2, U$3.3 (FB)
VFB3: R5.1, R6.2, U$5.3 (FB)
VFB4: R7.1, R8.2, U$7.3 (FB)
VFB5: R9.1, R10.2, U$9.3 (FB)
V_USB2: C24.1, IC1.12 (VCC), U1.VBUS1 (VBUS)
V_USB_CHG: C12.1, R38.1, U3.VBUS1 (VBUS), U$13.31 (UVCC), U$14.4 (VDD), U$21.1 (A), U$22.1 (A), U$23.1 (A), U$24.1 (A), U$25.1 (A)
XTAL1: C22.2, Q3.2, U2.36 (PR0)
XTAL2: C23.2, Q3.1, U2.37 (PR1)

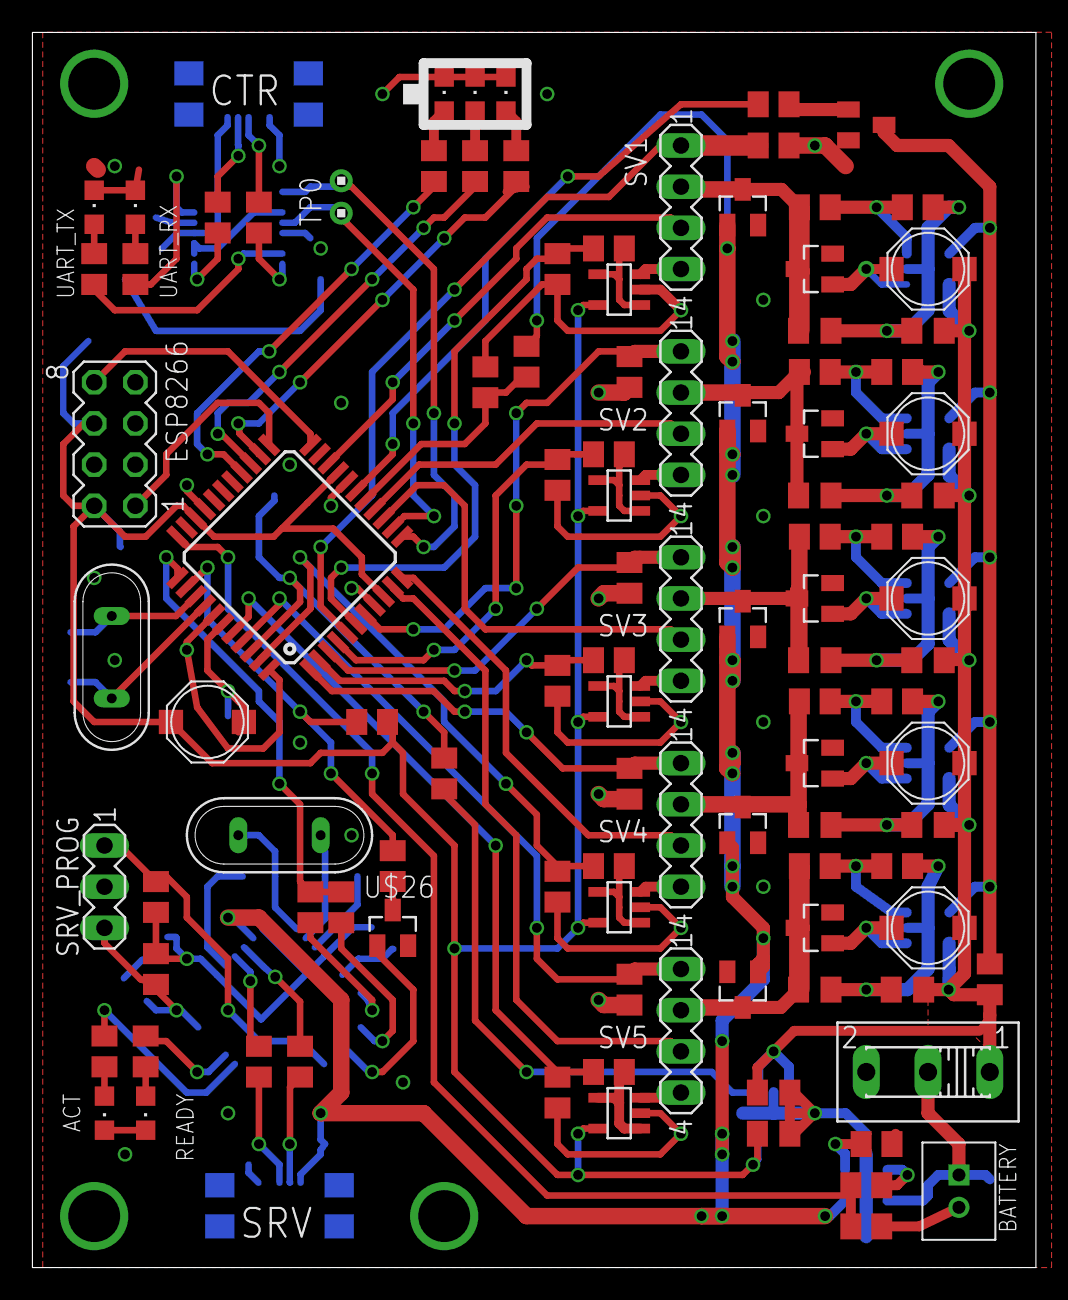
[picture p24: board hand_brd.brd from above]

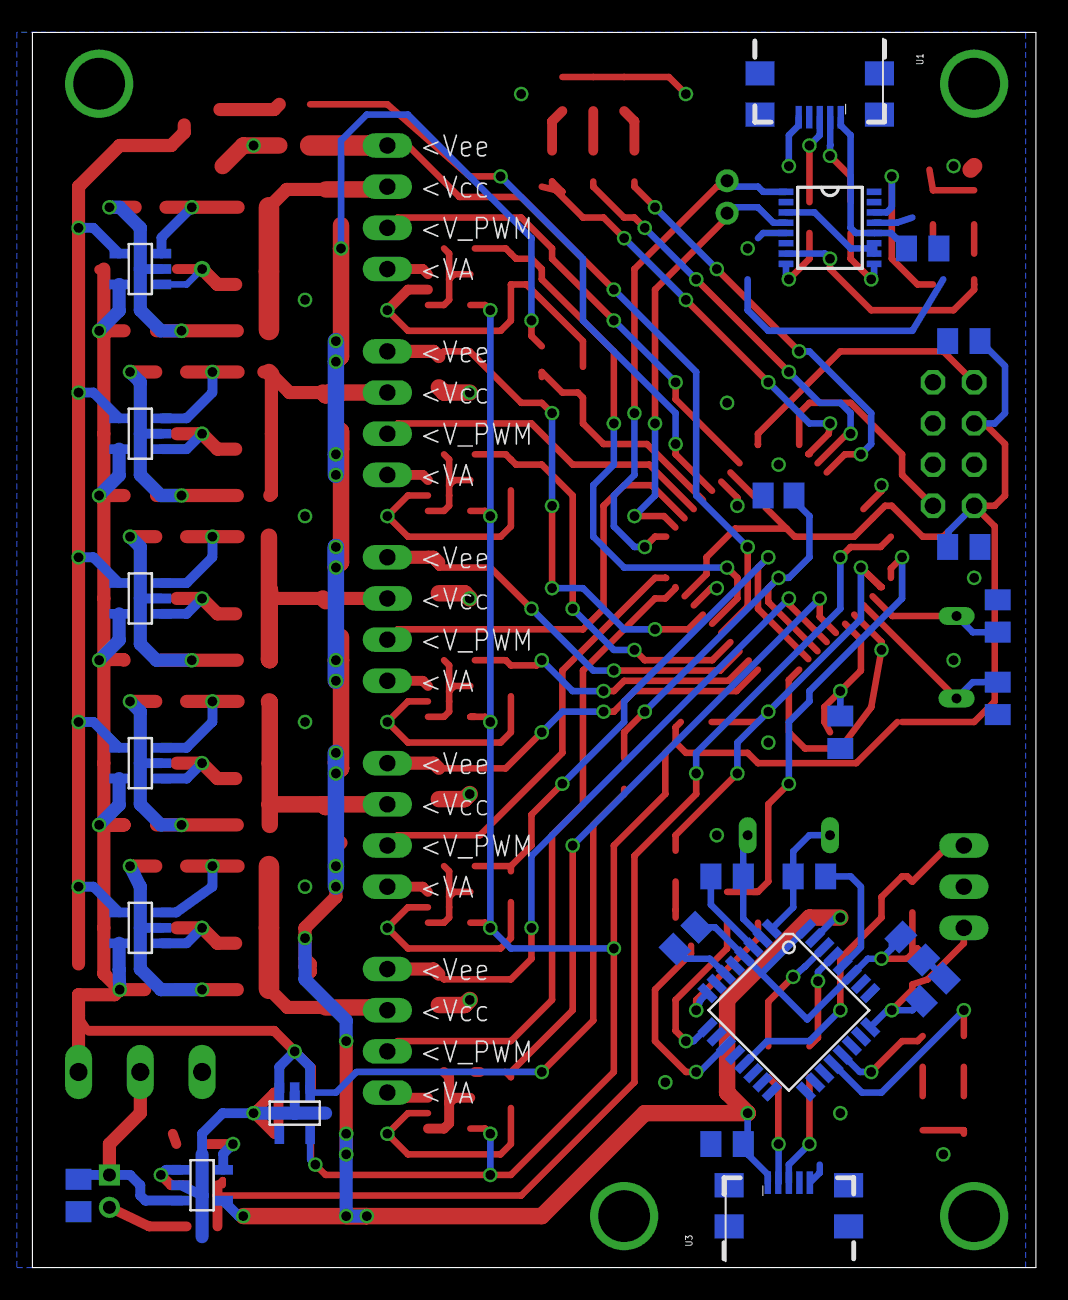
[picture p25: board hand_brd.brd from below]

Board: 2 copper layers, 61.9 x 76.2 mm, 130 parts (25 on the bottom side), 96 nets.

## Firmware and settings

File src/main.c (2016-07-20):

/**
 *
 *
 * Copyright (C) 2015 Paolo Scaramuzza <paolo.scaramuzza@ipol.gq>
 */
#include "include/board.h"
#include "include/avr_compiler.h"
//#include "include/pmic_driver.h"
#include "include/clksys_driver.h"

#include "include/adc_driver.h"
#include "include/esp_driver.h"
#include "include/serio_driver.h"
#include "include/servo_driver.h"
#include "include/battery_driver.h"

/**
 * Firmware entry point
 */
int main( void )
{
	/*
	 * HARDWARE INITIALIZATION
	 */
	CLKSYS_XOSC_Config(OSC_FRQRANGE_12TO16_gc, false,
			OSC_XOSCSEL_XTAL_256CLK_gc);
	CLKSYS_Enable(OSC_XOSCEN_bm);
	do {} while ( CLKSYS_IsReady(OSC_XOSCRDY_bm) == 0);
	CLKSYS_Main_ClockSource_Select(CLK_SCLKSEL_XOSC_gc);

	ADC_init();
	servo_init();
	battery_init();
	serio_init();
	esp_init();

	// Enable all interrupts
	PMIC.CTRL = PMIC_HILVLEN_bm | PMIC_MEDLVLEN_bm | PMIC_LOLVLEN_bm;
	sei();

	serio_putString("\r\nRA Thing v0.0 READY\r\n> "); // TODO make it a prompt
	/*
	 * main loop: listens for comands and executes them
	 */
	while (1) {
		union wifiCommand cmd = esp_getCommand(true);

		serio_putChar('C');
		serio_putChar(cmd.field.command + 48);

		serio_putString(" S");
		serio_putChar(cmd.field.servo + 48);

		serio_putString(" D");
		serio_putChar(cmd.field.data);
		serio_putString("\r\n");

		switch (cmd.field.command)
		{
			case WIFI_SET_MODE:
				if (cmd.field.data == WIFI_MODE_FOLLOW) {
					servo_setMode(FOLLOW);
					esp_sendCommand(cmd);
				} else if (cmd.field.data == WIFI_MODE_ANGLE) {
					servo_setMode(ANGLE);
					esp_sendCommand(cmd);
				} else if (cmd.field.data == WIFI_MODE_HOLD) {
					servo_setMode(HOLD);
					esp_sendCommand(cmd);
				}
				break;

			case WIFI_SET_ANGLE:
				servo_setAngle(cmd.field.servo, cmd.field.data);
				esp_sendCommand(cmd);
				break;

			case WIFI_SET_CURRENT:
				servo_setCurrent(cmd.field.servo, cmd.field.data);
				esp_sendCommand(cmd);
				break;

			case WIFI_SET_SPEED:
				servo_setSpeed(cmd.field.servo, cmd.field.data);
				esp_sendCommand(cmd);
				break;

			case WIFI_GET_ANGLE: // command is the same, with payload
				cmd.field.data = ADC_getServoAngle(cmd.field.servo);
				esp_sendCommand(cmd);
				break;

			case WIFI_GET_CURRENT:
				cmd.field.data = ADC_getServoCurrent(cmd.field.servo);
				esp_sendCommand(cmd);
				break;

			case WIFI_GET_SPEED:
				cmd.field.data = servo_getSpeed(cmd.field.servo);
				esp_sendCommand(cmd);
				break;
		}
	}
}

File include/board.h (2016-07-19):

/**
 * Global configuration file for the board. All the compile-time options go here
 *
 * Copyright (C) 2016 Paolo Scaramuzza <paolo.scaramuzza@ipol.gq>
 */

#ifndef BOARD_H
#define BOARD_H

	#include <stdint.h>

	/**
	 * Clock configuration
	 */
	// CPU clock frequency. USed for timing and other stuff
	#define F_CPU           16000000UL
	
	/**
	 * Various hardware assignments
	 */
	#define ESP_USART          USARTD0
	#define ESP_USART_DRE_vect USARTD0_DRE_vect
	#define ESP_USART_RXC_vect USARTD0_RXC_vect

	#define SERIO_USART          USARTC0
	#define SERIO_USART_DRE_vect USARTC0_DRE_vect
	#define SERIO_USART_RXC_vect USARTC0_RXC_vect

	#define BATTERY_VOLTAGE_PIN ADC_CH_MUXPOS_PIN0_gc
	#define ADC_NEG_PIN         ADC_CH_MUXNEG_PIN4_gc
	/**
	 * Define where the servos are connected and their function
	 */
	#define THUMB_FINGER  0
	#define INDEX_FINGER  1
	#define MIDDLE_FINGER 2
	#define RING_FINGER   3
	#define PINKY_FINGER  4

	#define THUMB_TIMER   TCD0
	#define thumbSetCompare(_comp)  TC_SetCompareA( &THUMB_TIMER, _comp )

	#define INDEX_TIMER   TCC1
	#define indexSetCompare(_comp)  TC_SetCompareB( &INDEX_TIMER, _comp )

	#define MIDDLE_TIMER  TCC1
	#define middleSetCompare(_comp) TC_SetCompareA( &MIDDLE_TIMER, _comp )

	#define RING_TIMER    TCC0
	#define ringSetCompare(_comp)   TC_SetCompareB( &RING_TIMER, _comp )

	#define PINKY_TIMER   TCC0
	#define pinkySetCompare(_comp)  TC_SetCompareA( &PINKY_TIMER, _comp )

	#define THUMB_CURRENT_PIN  ADC_CH_MUXPOS_PIN9_gc
	#define THUMB_ANGLE_PIN    ADC_CH_MUXPOS_PIN10_gc

	#define INDEX_CURRENT_PIN  ADC_CH_MUXPOS_PIN11_gc
	#define INDEX_ANGLE_PIN    ADC_CH_MUXPOS_PIN8_gc

	#define MIDDLE_CURRENT_PIN ADC_CH_MUXPOS_PIN7_gc
	#define MIDDLE_ANGLE_PIN   ADC_CH_MUXPOS_PIN6_gc

	#define RING_CURRENT_PIN   ADC_CH_MUXPOS_PIN5_gc
	#define RING_ANGLE_PIN     ADC_CH_MUXPOS_PIN3_gc

	#define PINKY_CURRENT_PIN  ADC_CH_MUXPOS_PIN1_gc
	#define PINKY_ANGLE_PIN    ADC_CH_MUXPOS_PIN0_gc

	/**
	 * Commands supported through the wifi link
	 */
	union wifiCommand
	{
		struct
		{
			uint8_t command : 4;
			uint8_t servo : 4;
			uint8_t data;
		}field;
		uint16_t raw;
	};
	union wifiCommand_le // Little-endian version
	{
		struct
		{
			uint8_t data;
			uint8_t command : 4;
			uint8_t servo : 4;
		}field;
		uint16_t raw;
	};
	#define WIFI_SET_MODE    0x01
	#define WIFI_SET_ANGLE   0x02
	#define WIFI_SET_CURRENT 0x03
	#define WIFI_SET_SPEED   0x04

	#define WIFI_GET_ANGLE   0x05
	#define WIFI_GET_CURRENT 0x06
	#define WIFI_GET_SPEED   0x07

	#define WIFI_MODE_FOLLOW 0x00
	#define WIFI_MODE_ANGLE  0x01
	#define WIFI_MODE_HOLD   0x02
#endif

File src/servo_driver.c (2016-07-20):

/**
 *
 *
 * Copyright (C) 2016 Paolo Scaramuzza <paolo.scaramuzza@ipol.gq>
 */
#include "include/board.h"
#include "include/avr_compiler.h"
#include "include/TC_driver.h"
#include "include/adc_driver.h"

#include "include/servo_driver.h"
#include "include/serio_driver.h"
#include "include/utils.h"

static volatile servo_state_t status = FOLLOW; // start in a safe mode

struct servo_data_t
{
	servo_state_t status;
	uint16_t controlPWM; // Value to send to the CC module, multiplied by
	                     // SPEED_DIVIDER to get fractional speed
	uint8_t  maxCurrent_mA; // maximum allowed current
	uint8_t  targetAngle_deg; // angle to be reached
	uint8_t  speed; // speed of angle rotation
};
static struct servo_data_t sData[5];

void servo_init()
{
	PORTD.DIRSET = PIN0_bm;
	PORTC.DIRSET = PIN5_bm | PIN4_bm | PIN1_bm | PIN0_bm;

	TC_SetPeriod(&THUMB_TIMER, COMPARE_MAX);
	TC0_ConfigClockSource(&THUMB_TIMER, CLK_DIV);
	TC0_ConfigWGM(&THUMB_TIMER, TC_WGMODE_DS_T_gc);
	TC0_EnableCCChannels(&THUMB_TIMER, TC0_CCAEN_bm);
	TC0_SetCCAIntLevel(&THUMB_TIMER, TC_CCAINTLVL_MED_gc);

	TC_SetPeriod(&INDEX_TIMER, COMPARE_MAX);
	TC1_ConfigClockSource(&INDEX_TIMER, CLK_DIV);
	TC1_ConfigWGM(&INDEX_TIMER, TC_WGMODE_DS_T_gc);
	TC1_EnableCCChannels(&INDEX_TIMER, TC0_CCBEN_bm);
	TC1_EnableCCChannels(&MIDDLE_TIMER, TC0_CCAEN_bm); // on the same timer

	TC_SetPeriod(&RING_TIMER, COMPARE_MAX);
	TC0_ConfigClockSource(&RING_TIMER, CLK_DIV);
	TC0_ConfigWGM(&RING_TIMER, TC_WGMODE_DS_T_gc);
	TC0_EnableCCChannels(&RING_TIMER, TC0_CCBEN_bm);
	TC0_EnableCCChannels(&PINKY_TIMER, TC0_CCAEN_bm); // on the same timer

	// provide some safe default values
	for (int i = 0; i < 5; i++) {
		sData[i].status = FOLLOW;
		sData[i].controlPWM = SERVO_PWM_MIN * SPEED_DIVIDER;
		sData[i].targetAngle_deg = 0;
		sData[i].maxCurrent_mA = DEF_CURRENT_MA;
		sData[i].speed = 1;
	}
}
/**
 * Convert an angle in degrees into a valid capture-compare value
 */
inline uint16_t angle2comp(uint8_t angle)
{
	return SERVO_PWM_MIN + ((angle * 25) / 9) * 4; // (MAX-MIN) / 180
}

/**
 * Interrupt service routine. It transfers the requested servo angle to the PWM
 * subsystem, checking that the current does not exceed the threshold.
 *
 * TODO: maybe one for each servo group?
 */
ISR(TCD0_CCA_vect)
{
	for (int i = 0; i < 5; i++)
	{ // update the driving signal for each servo
		uint16_t compVal = sData[i].controlPWM;
		uint16_t targetComp = angle2comp(sData[i].targetAngle_deg)
			* SPEED_DIVIDER;
		uint8_t speed = sData[i].speed;
		uint8_t maxCurrent = sData[i].maxCurrent_mA;
		uint8_t actualAngle = ADC_getServoAngle(i);
		uint8_t actualCurrent = ADC_getServoCurrent(i);

		switch (sData[i].status)
		{
			case ANGLE:
				if (actualCurrent < maxCurrent) {
					if (compVal < targetComp) {
						compVal += speed;
						compVal = min(compVal, targetComp);
					} else if (compVal > targetComp) {
						compVal -= speed;
						compVal = max(compVal, targetComp);
					}
				} else {
					compVal = 0; // too much current. STOP!
				}
				break;

			case HOLD:
				// NOTE: I'm supposing the hand is closed when the servo goes
				// to 180 degrees and opened otherwhise
				if (actualCurrent < maxCurrent) {
					compVal++; // hold it slowly, yum!
					compVal = min(compVal, targetComp);
				} else {
					compVal -= 10;
					compVal = max(compVal, SERVO_PWM_MIN * SPEED_DIVIDER);
				}
				break;

			case FOLLOW:
				if ((compVal == 0) && (actualCurrent < 5))
				{ // compVal was zero so the current is negligible and the angle
				  // reading correct
					compVal = angle2comp(actualAngle) * SPEED_DIVIDER;
				} else {
					compVal = 0;
				}
				break;
		}

		if (compVal >= SERVO_PWM_MIN * SPEED_DIVIDER) // save only if valid
			sData[i].controlPWM = compVal;

		// set the capture-compare value to the correct servo
		compVal = compVal / SPEED_DIVIDER;
		switch (i) {
			case THUMB_FINGER:
				thumbSetCompare(compVal);
				break;

			case INDEX_FINGER:
				indexSetCompare(compVal);
				break;

			case MIDDLE_FINGER:
				middleSetCompare(compVal);
				break;

			case RING_FINGER:
				ringSetCompare(compVal);
				break;

			case PINKY_FINGER:
				pinkySetCompare(compVal);
				break;
		}
	}
}

void servo_setMode(const servo_state_t mode)
{
	if (status != FOLLOW) {
		status = mode;

		for (int i = 0; i < 5; i++) {
			sData[i].status = mode;
		}
	} else {
		status = mode;
		// avoid power surges by setting the status immediately.
		// wait for position / current / speed updates instead
	}
}

void servo_setAngle(const uint8_t servo_num, const uint8_t angle)
{
	if (servo_num > 4)
		return;

	uint8_t a = max(angle, 1); // setting angle to 0 may screw the control
	                           // algorithm
	a = min(a, 180);

	sData[servo_num].targetAngle_deg = a;
	sData[servo_num].status = status;
}

void servo_setCurrent(const uint8_t servo_num, const uint8_t current_mA)
{
	if (servo_num > 4)
		return;

	sData[servo_num].maxCurrent_mA = current_mA;
	sData[servo_num].status = status;
}

void servo_setSpeed(const uint8_t servo_num, const uint8_t speed)
{
	if (servo_num > 4)
		return;

	sData[servo_num].speed = speed;
	sData[servo_num].status = status;
}

uint8_t servo_getAngle(const uint8_t servo_num)
{
	uint16_t actPWM = sData[servo_num].controlPWM / SPEED_DIVIDER;
	actPWM -= SERVO_PWM_MIN;
	return (actPWM * 9) / 100;
}

uint8_t servo_getSpeed(const uint8_t servo_num)
{
	uint8_t current = ADC_getServoCurrent(servo_num);

	if ((current > 10) && (current < sData[servo_num].maxCurrent_mA))
		return sData[servo_num].speed;

	return 0;
}

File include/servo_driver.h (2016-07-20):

/**
 *
 *
 * Copyright (C) 2015 Paolo Scaramuzza <paolo.scaramuzza@ipol.gq>
 */
#ifndef SERVO_DRIVER_H
#define SERVO_DRIVER_H

	#include <stdint.h>

	/**
	 * Driver operating modes:
	 *
	 * ANGLE:  The servo tries to go to the desired angle with a given speed.
	 *         If a current threshold is crossed the driving signal is
	 *         momentarily disabled
	 *
	 * HOLD:   The servo tries to hold an object into the hand, applying the
	 *         desired force. This means that a given angle is kept as long as
	 *         the current stays below a threshold. If the threshold is crossed
	 *         the hand is opened slightly.
	 *
	 * FOLLOW: The driver does nothing. It sends pulses to the servo trying to
	 *         follow the position in which the operator is putting this hand's
	 *         fingers.
	 */
	typedef enum { ANGLE, HOLD, FOLLOW } servo_state_t;

	/**
	 * Configuration directives
	 */
	// Those afferct the PWM frequency and resolution. See the XMEGA manual
	#define COMPARE_MAX    19999 // sets the servo frequency to 50Hz
	#define CLK_DIV        TC_CLKSEL_DIV8_gc
	// Minimun output value for servo PWM
	#define SERVO_PWM_MIN  500
	// Maximum output value for servo PWM
	#define SERVO_PWM_MAX  2500
	// Divider for the speed, used to slow down servo motion
	#define SPEED_DIVIDER  2
	// Default maximum current in mA
	#define DEF_CURRENT_MA 250

	/**
	 * Initialize the hardware components needed for servo operation
	 */
	void servo_init();

	/**
	 * Choose the operating mode for this dirver
	 */
	void servo_setMode(const servo_state_t mode);

	/**
	 * Set some angle to the desired servo.
	 * Angle must be between 0 and 180. Values outside such range will be
	 * cropped.
	 * This function fails silently if servo_num is not valid
	 */
	void servo_setAngle(const uint8_t servo_num, const uint8_t angle);

	/**
	 * Set the servo current in milliamperes.
	 * This function fails silently if servo_num is not valid
	 */
	void servo_setCurrent(const uint8_t servo_num, const uint8_t current_mA);

	/**
	 * Set the speed at which te servo rotates when in ANGLE mode. This speed is
	 * a value which will be summed to the current angle until the goal is
	 * reached.
	 * This function fails silently if servo_num is not valid
	 */
	void servo_setSpeed(const uint8_t servo_num, const uint8_t speed);

	/**
	 * Return the current speed for the chosen servomotor
	 *
	 * NOTE: Choosing an invalid servo number may result in erratic behaviour.
	 */
	uint8_t servo_getSpeed(const uint8_t servo_num);
	/**
	 * Return the current angle for the chosen servomotor
	 *
	 * NOTE: Choosing an invalid servo number may result in erratic behaviour.
	 */
	uint8_t servo_getAngle(const uint8_t servo_num);
#endif

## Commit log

2016-06-25 Add schematic and layout
    [bom.ods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]
2016-06-25 Prepare the ground for using multiple servos
2016-06-26 Enable three different operating modes for the servo driver.
2016-06-26 The correct value for the CC register was not always set+
    [servo_driver.c]
2016-06-29 New protocol! Not always working due to parsing issues
    [board.h, main.c, servo_driver.c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]
2016-07-02 Fix wrong USB model
    [hand_brd.brd, hand_brd.sch]
2016-07-03 Create gerber files from the updated board
    [hand_brd.GBL, hand_brd.GBO, hand_brd.GBP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]
2016-07-03 The serio driver is now able to send data through the serial port
2016-07-03 Make the driver status variable volatile
2016-07-03 Recognize when no servo is supplied as an argument and the user is trying to modify some parameters
2016-07-09 make speed fractional to slow down servo motion
2016-07-09 Add commands for reading servo variables from the wifi link
2016-07-09 Send commands from the board to the controlling application using WiFi
2016-07-12 Fix data sending which was not working due to a typo and a wrong interrupt level
    [board.h, main.c]
2016-07-13 rework esp_driver a bit in order to use interrupts
    [board.h]
2016-07-14 fix issues with the WiFi driver. Now it should work correctly
    [main.c, wifimon.c]
2016-07-15 update BOM
    [bom.ods]
2016-07-16 Add missing diode
    [hand_brd.brd, hand_brd.sch]
2016-07-17 Port the code to the new board
2016-07-17 Use the shiny-new ADC driver with the old servo driver
2016-07-17 Add battery driver to control the carge status
2016-07-18 Fix wrong detection of low battery and disable the converters when external powered
    [bom.ods]
2016-07-18 Forgotten to add the battery driver files. Here they are
2016-07-18 Remove unused connection for disabling the boost converters and shuffle things around a bit to have a better ground plane
    [hand_brd.brd, hand_brd.sch]
2016-07-19 Enable the external crystal oscillator
    [adc_driver.c, adc_driver.h, battery_driver.c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]
2016-07-19 Fix missing port initialization
    [adc_driver.c, battery_driver.c, main.c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]
2016-07-19 Add clksys drivers
2016-07-19 Try to fix the current measuring with no result
    [adc_driver.c, adc_driver.h]
2016-07-20 Fix TheADC driver a bit. I have still no clue why the measurements seem to be incorrect
    [adc_driver.c, main.c]
2016-07-20 Fix missing curly braces
    [main.c]
2016-07-20 Avoid power surges by setting the status of each servo immediately. Wait for updates instead
    [servo_driver.c]
2016-07-20 Fail silently if setting values on an invalid servo
    [servo_driver.c, servo_driver.h]
2016-07-20 Increase default maximum current
2016-07-20 Revert changes to the ADC driver. Still not working :(
    [adc_driver.c]
